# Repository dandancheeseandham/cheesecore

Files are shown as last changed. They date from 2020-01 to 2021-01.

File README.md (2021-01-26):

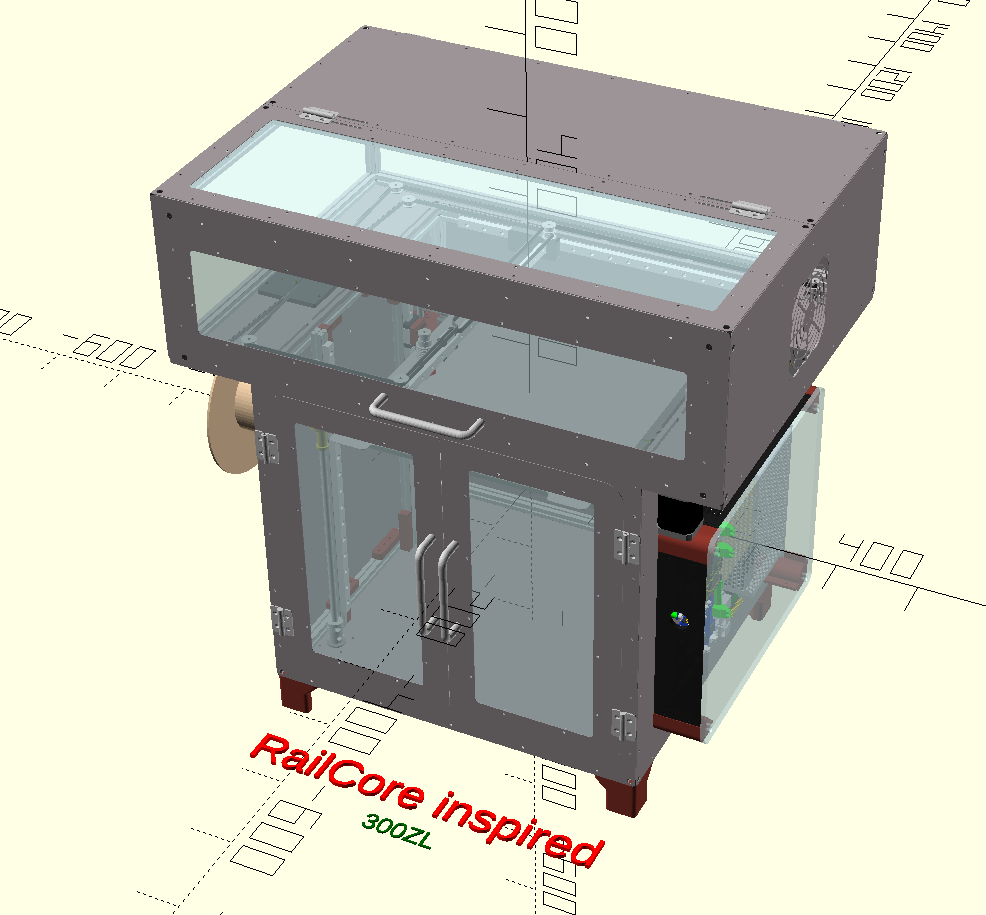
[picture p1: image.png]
Image of cheesecore


# cheesecore - a RailCore II inspired build

This OpenSCAD program has been developed to emulate, and be fully compatible with the RailCore II, but to extend it with parametric functionality. 
While it should be fully compatiable, please note that it is **not a RailCore II**. Because of this **please do not** direct questions about this OpenSCAD code or its models or parts to Tony Akens or J.Steve White. Please discuss with Dan White on Facebook, or idealy cheeseandham on the RailCore Discord.

If you stick with 12mm rails, everything should be fully compatible, but to protect myself I will say **mixing this design with a RailCore II is at your own risk**. 

cheesecore has been developed by cheeseandham / Dan White.

## Initial Goals

To make a RailCore2-compatible parametric OpenSCAD model that includes as standard:- 
 * doors
 * halo
 * top enclosure

The parametrics are to be able to change parameters such as:-
 * frame size (height,width,length) and panel/door thickness
 * extrusion size 
 * rail length and profile (on Z especially) e.g. MGN15
 * lead screw width
 * front window size 
 * electronic box size and electronics placement
 * NEMA stepper motor type (e.g. 17 or 23)

Where possible we stay within the RailCore ecosystem in regards to:-
 * Y carriage - keep 12mm rail on the Y (highest priority)
 * Bed - bed is modifiable
 * Keeping 8mm leadscrews and 12mm rails on Z. This is modifiable.
 
In order to take advantage of existing parts. However these parameters may also be changed - it should be understood that this especially will break compatibility with current machined parts.

## To Do
 * allow >4040 extrusion e.g. 3060 as well as ensuring all screwholes for extrusions are changed.
 * develop main parts of the hotend ecosystem.
 * export a BOM from cheesecore.
 * tidy and optimise the model and code.

### Secondary Goals

1. Adding a RPi as standard, for additional functionality.
 * Bossa for emergency Duet flashing
 * USB and Octoprint (extra features and the ability to communicate with the Duet with a network issue)
 * Extra hardware that a Duet can't support.
 * Automated backups and a simple restore procedure.
2. Include a "advanced user" Duet config and setup.
3. The ability to make modifications and improve the design where appropriate.
The base RailCore design should always be available, and options can be switched on and off as required.
4. Minimize printed part content - metals behave more predictably, espeicially at higher temperatures.
5. Safety - Add software and hardware means (such as TCO's)
6. Aid and ease assembly - anything that can reduce issues in getting it printing reliably. Such as additional parts to ensure squareness of extrusion and rails.

## To use

Some OpenSCAD experience is useful, but if you're comfortable with code in general you should be OK.

 * open a "make*.scad" file to open a whole model.
 * All variables are held in config.scad
 * Theming held in colors.scad and set in prefs.scad
 * Configurations for models are held in models_standard.scad and models_experimentals.scad
 * to play with a whole model, use make_customcore.scad and edit the variables in models_experimental.scad and config.scad regarding the custom model and open with make_customcore.scad
 * core.scad is called to render the model, so you can easily omit parts by using a * to stop it being rendered by editing core.scad/
 * If you open any individual scad part, it will render as per the model in demo.scad , and therefore settings for it in the configuations (models_standard.scad and models_experimentals.scad) (if a individual file contains many parts, you can change its behaviour via editting the demo modile in this part.
 * use the scripts in the build/scripts folder to export the models - this will dump dxfs, stls and renders into the artifacts and renders folders. (any files in artifacts and renders may be deleted as they are easily recreated)
 * hotend is not part of the model yet. It assumes a 12mm rail on Y and RailCore hotend ecosystem at this time.
 * in the build directory are the files to export individual parts.
 * to export all parts, or all parts for all models, just run the appropriate script in build/scripts for your operating system (.cmd for windows, and .sh for mac/linux).

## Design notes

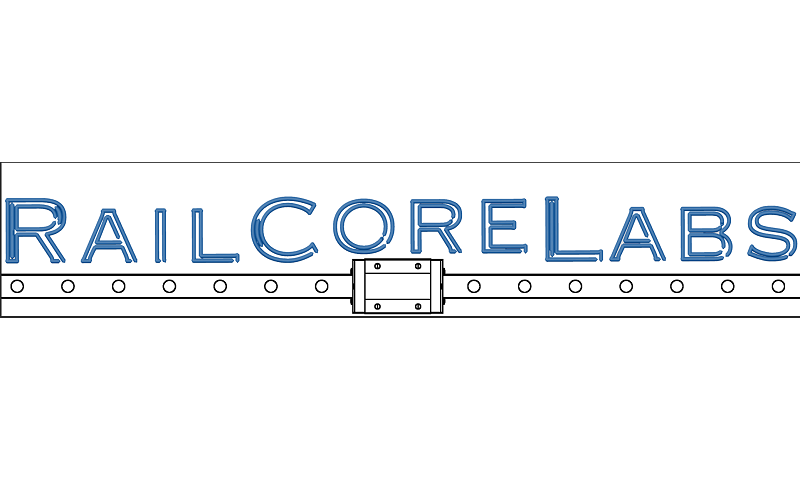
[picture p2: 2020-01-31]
accessories/PanelDue/RailCoreLabs_small.bmp

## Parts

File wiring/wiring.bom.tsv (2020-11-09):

Item | Qty | Unit | Designators
Connector, Delta BFB0524HH Fan, 2 pins | 1 |  | X20
Connector, Ferrule, crimp | 6
Connector, Insulated Female Spade Connector, 6.3 x 0.8mm Tab Size, insulated, 1 pins | 3 |  | X11, X13, X9
Connector, Insulated Ring Terminal, M4 Stud Size, insulated, 1 pins | 11 |  | X1, X10, X12, X2, X22, X3, X4, X5, X6, X7, X8
Connector, Molex 50-57-9404, female, 4 pins | 1 |  | X21
Connector, Molex 70107-0003, male, 4 pins | 1 |  | X18
Connector, Molex KK 254, female, 2 pins | 1 |  | X17
Connector, Molex KK 254, female, 3 pins | 2 |  | X14, X16
Connector, OMRON D2F-01F, Microswitch, 3 pins | 2 |  | X15, X19
Connector, Stripped Wire, 10mm | 9
Wire, 0.25 mm², BK | 1.1 | m | W15, W16
Wire, 0.25 mm², GN | 2.1 | m | W14, W15, W16
Wire, 0.25 mm², GY | 2.1 | m | W14, W15, W16
Wire, 0.25 mm², RD | 1.1 | m | W15, W16
Wire, 1.5 mm², BN | 0.89 | m | W1, W5, W6
Wire, 1.5 mm², BU | 0.7 | m | W1, W10, W11
Wire, 1.5 mm², GN | 2.05 | m | W12, W13, W17, W4
Wire, 1.5 mm², GY | 1.0 | m | W2, W3, W7, W8, W9

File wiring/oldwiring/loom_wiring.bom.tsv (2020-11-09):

Item | Qty | Unit | Designators
Connector, 0.25" Quick Disconnect / 6.3mm female spade F/I terminal / Insulated Crimp Receptacle, insulated, 1 pins | 3 |  | X11, X13, X9
Connector, Delta BFB0524HH Fan, 2 pins | 1 |  | X20
Connector, Ferrule, crimp | 6
Connector, Molex 50-57-9404, female, 4 pins | 1 |  | X21
Connector, Molex 70107-0003, male, 4 pins | 1 |  | X18
Connector, Molex KK 254, female, 2 pins | 1 |  | X17
Connector, Molex KK 254, female, 3 pins | 2 |  | X14, X16
Connector, OMRON D2F-01F, Microswitch, 3 pins | 2 |  | X15, X19
Connector, Ring Terminal RV1.25-5S Stud size 10, insulated, 1 pins | 11 |  | X1, X10, X12, X2, X22, X3, X4, X5, X6, X7, X8
Connector, Stripped Wire, 10mm | 9
Wire, 16 AWG, BK | 1.5 | m | W1, W2, W3, W7, W8, W9
Wire, 16 AWG, GN | 2.05 | m | W12, W13, W17, W4
Wire, 16 AWG, RD | 0.89 | m | W1, W5, W6
Wire, 16 AWG, WH | 0.2 | m | W10, W11
Wire, 24 AWG, BK | 3.2 | m | W14, W15, W16
Wire, 24 AWG, GN | 2.1 | m | W14, W15, W16
Wire, 24 AWG, RD | 1.1 | m | W15, W16

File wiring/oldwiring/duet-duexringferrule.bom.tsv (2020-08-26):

Item | Qty | Unit | Designators
Connector, Ferrule, crimp, 2.0 mm², YE | 1
Connector, Ring#8, crimp, 1 pins | 1 |  | DUET
Cable, 1 x 0.34 mm² | 0.5 | m | BED_SSR3

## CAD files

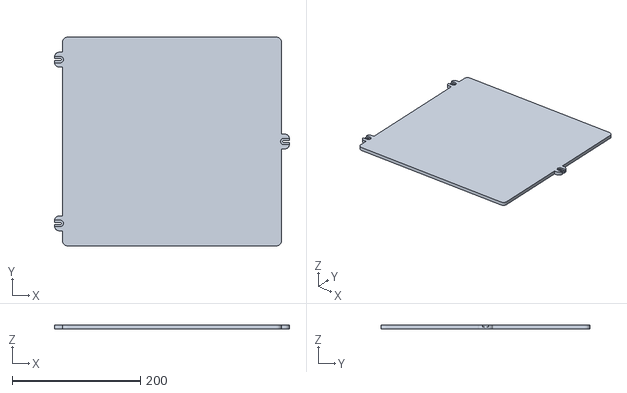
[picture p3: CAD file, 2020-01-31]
accessories/prusa_slicer_configs/railcore.stl
366.0 x 325.0 x 6.35

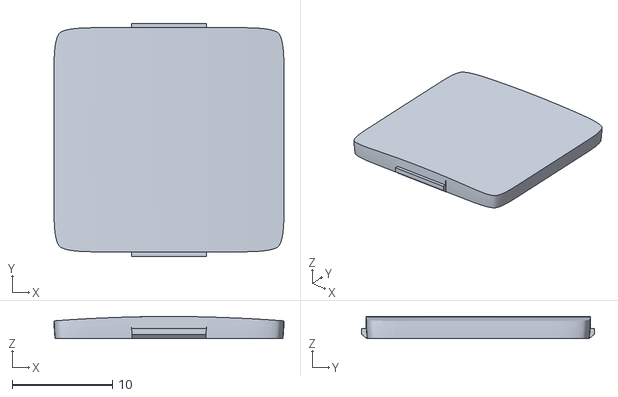
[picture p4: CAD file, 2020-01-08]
nopscadlib/vitamins/microview/GKM-002_R05_CHIP_UPPER_HOUSING-1.STL
22.9 x 23.2 x 2.20

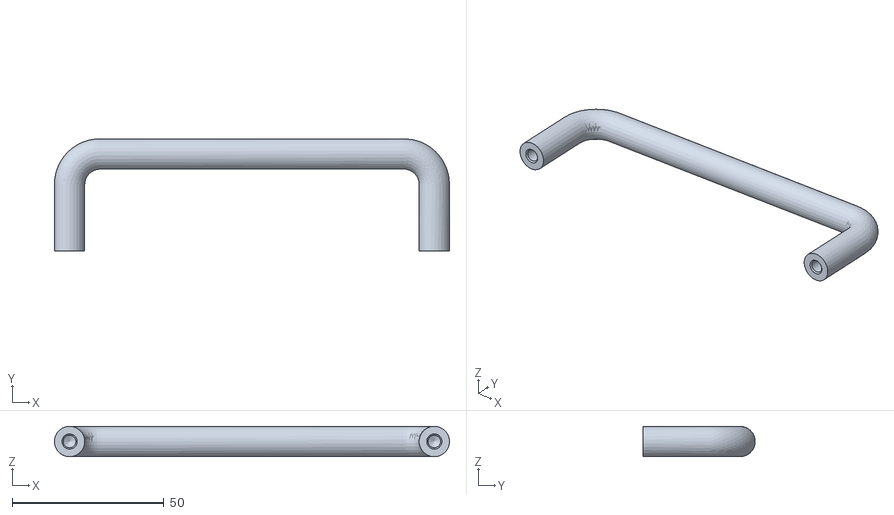
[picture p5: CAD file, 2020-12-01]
UWAN10-120-27.stl
130.0 x 37.0 x 10.0

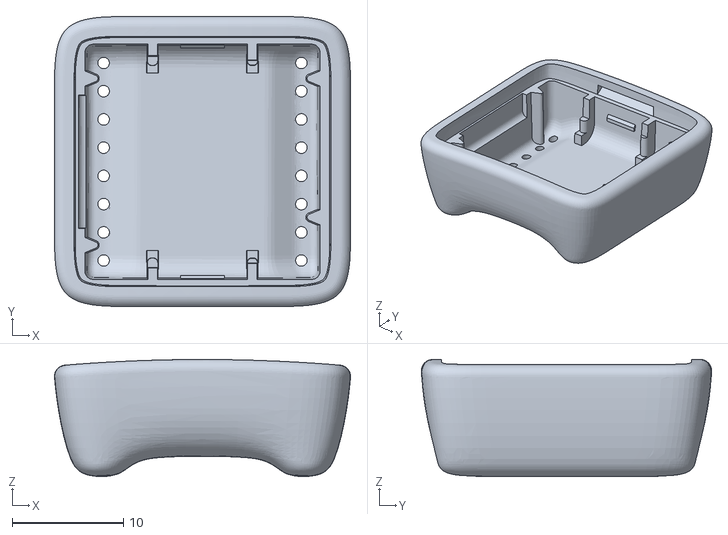
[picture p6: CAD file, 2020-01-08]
nopscadlib/vitamins/microview/GKM-003_R05_CHIP_LOWER_HOUSING.STL
26.7 x 26.1 x 10.5

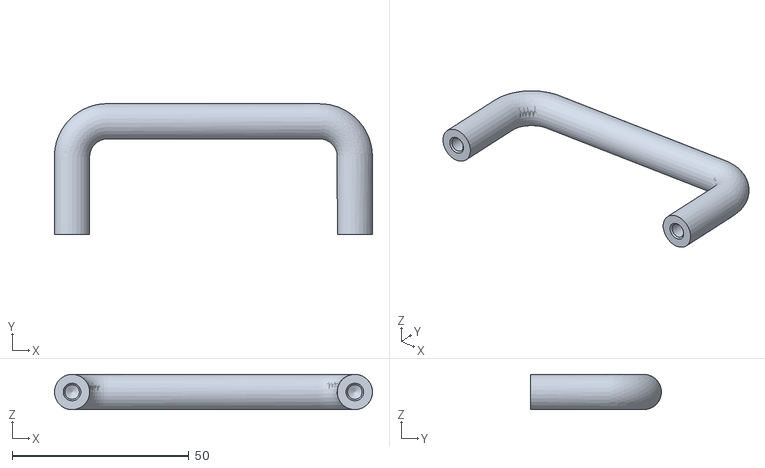
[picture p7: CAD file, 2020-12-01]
UWAN10-80-27.stl
90.0 x 37.0 x 10.0

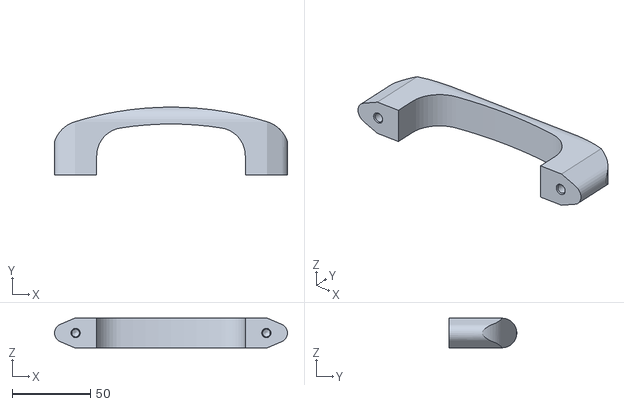
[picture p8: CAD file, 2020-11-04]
HHDS122.stl
149.0 x 43.3 x 19.0

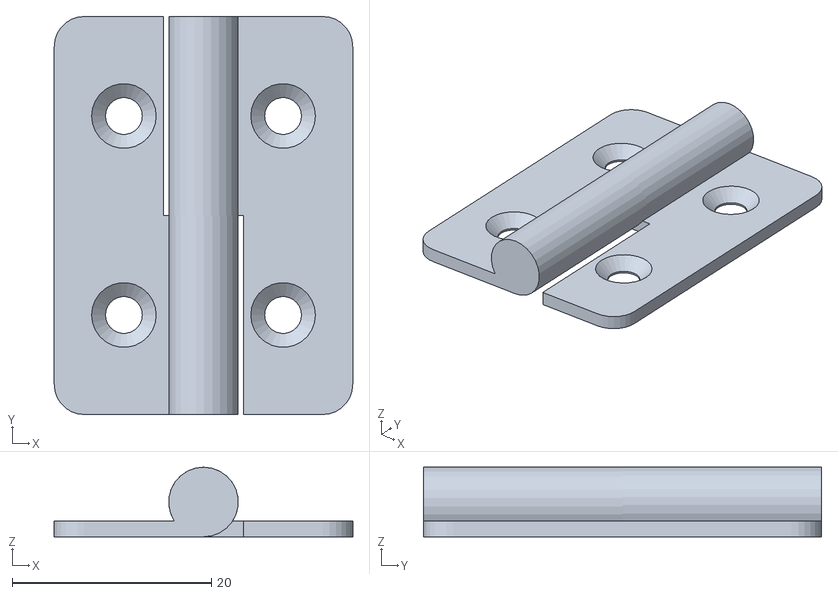
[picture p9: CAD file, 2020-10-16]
B_1075_R.stl
30.0 x 40.0 x 7.00

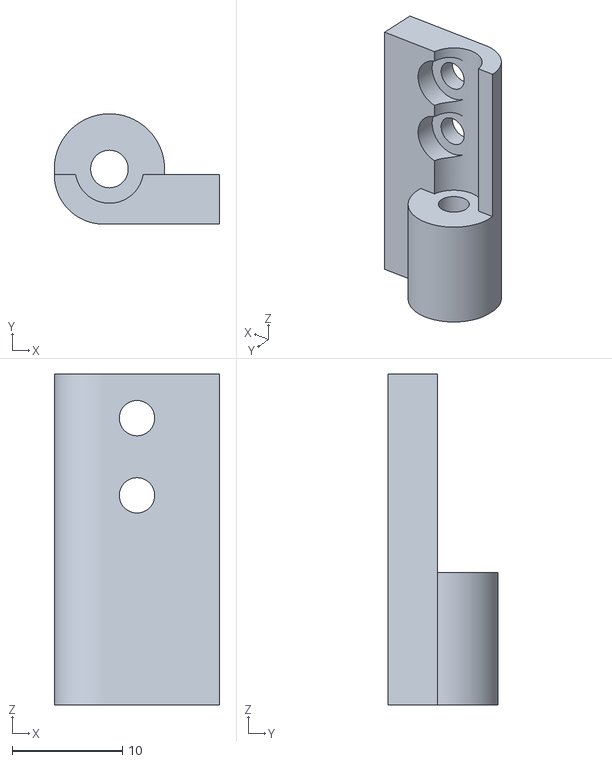
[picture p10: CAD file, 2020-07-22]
HINGE_1.stl
15.0 x 10.00 x 30.0

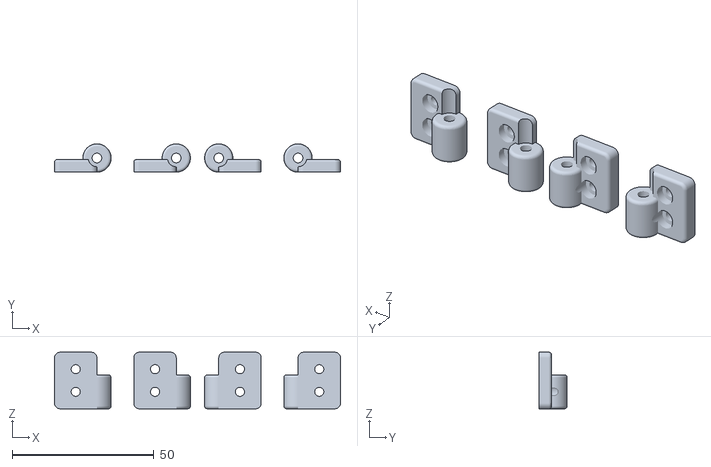
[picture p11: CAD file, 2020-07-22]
HINGE_2.stl
101.0 x 10.0 x 20.0

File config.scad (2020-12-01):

// vim: set nospell:
include <colors.scad>
include <prefs.scad>
include <constants.scad>
use <validation.scad>
include <nopscadlib/vitamins/rails.scad>
include <nopscadlib/vitamins/stepper_motors.scad>

// *************************************************************************************************************************************************

// FRAME - either specify frame size complete or specify extrusion sizes and addon the corner cubes e.g. [15*2,15*2,15*2] for 15mm corner cubes.
//                        sizeX sizeY sizeZ
//Standard
frame_original_rc150mini= [270, 270, 270] + [15*2,15*2,15*2]; // defining extrusion size and then adding frame corner cubes
frame_original_rc250zl  = [400, 370, 360] + [15*2,15*2,15*2];
frame_original_rc300zl  = [460, 425, 415] + [15*2,15*2,15*2];
frame_original_rc300zlt = [460, 425, 715] + [15*2,15*2,15*2];
//Experimental
frame_rc300_custom      = [490, 500, 460];
//Test-ground
frame_rc300zl4040       = [590, 555, 545];


// PANEL - Sides, halo and doors.
//                                  Panel        panel    Extend      Panel Screw  max panel    Bottom
//                                thickness      radius   panels      Offset       screw space  braces?
//Standard
panels_imperial_250zl   = ["PANELS",0.25 * inch,  5,      0,0,0,      42.5,          101,       false];
panels_imperial         = ["PANELS",0.25 * inch,  5,      0,0,0,      50,            100,       true];
panels_metric           = ["PANELS",6,            5,      0,0,0,      50,            100,       true];
panels_aluminium        = ["PANELS",4,            5,      0,0,0,      50,            100,       false];
panels_steel            = ["PANELS",0.8,          5,      0,0,0,      50,            100,       false];
//Experimental
panels_custom           = ["PANELS",6,            5,      150,0,53,   55,            100,       false];
panels_cheese           = ["PANELS",3,            3,      95*2,0,53,  50,            100,       false];
function fitting_error()= 0.25; //reduce panels by this size to account for whatever +- cutting error there may be
function feetheight()   = $feet_depth;

// FRONT WINDOW / DOOR
//                            name                sizeXY   radius   offset    door thickness
//Standard
front_window_original_150mini = ["WINDOW_TYPE", [245, 210], 10,     [0, 5],   0.25 * inch];
front_window_original_250zl   = ["WINDOW_TYPE", [370, 335], 10,     [0, 5],   0.25 * inch];
front_window_original_300zl   = ["WINDOW_TYPE", [420, 385], 10,     [0, 5],   6];
front_window_cheesecore       = ["WINDOW_TYPE", [420, 385], 10,     [0, 5],   0.8];
front_window_original_300zlt  = ["WINDOW_TYPE", [410, 645], 10,     [0, 0],   6];
//Experimental
front_window_custom           = ["WINDOW_TYPE", [420, 385], 10,     [0, 0],   6];

// RAILS
//                           sizeX  Xtype  sizeY  Ytype    sizeZ Ztype
//Standard
rails_original_rc150mini = [[245, MGN12], [245, MGN12], [245, MGN12]];
rails_original_rc250zl   = [[350, MGN12], [350, MGN12], [350, MGN12]];
rails_original_rc300zl   = [[400, MGN12], [400, MGN12], [400, MGN12]];
rails_original_rc300zlt  = [[400, MGN12], [400, MGN12], [700, MGN12]];
//Experimental
rails_misumi_395         = [[395, MGN12], [395, MGN12], [395, MGN12]];
rails_misumi_420         = [[420, MGN12], [420, MGN12], [420, MGN12]];
rails_misumi_420XY_470Z  = [[420, MGN12], [420, MGN12], [470, MGN12]];
rails_rc300zlt_high_temp = [[400, MGN12], [400, MGN12], [700, MGN15]];
// Test-ground (can be deleted)
rails_300zl_4040         = [[500, MGN15], [500, MGN12], [500, MGN15]];
rails_custom             = [[420, MGN9] , [445, MGN12], [420, MGN15]];

// ELECTRONICS BOX ALONG WITH  & ELECTRONICS & CABLE PLACEMENT -  placement of parts on right panel with X/Y as centre
//                                                      DIMENSIONS               |       POSITIONS
//                           name        sizeX  sizeZ  depth thick, move lasercut   cable_bundle      DuetE            Duex            PSU        SSR            RPi
//                                                                  box
//Standard                                                         down
elecbox_original_rc150mini= ["ELEC.BOX", 298.9, 238.9, 60 ,   6,    25,    true,   [-84,126.5,0], [-84.82,50.5,0], [-84.82,-59.5,0], [90,30,0], [45,-115,0] , [90,30,0]] ;
elecbox_original_rc250zl  = ["ELEC.BOX", 298.9, 238.9, 60 ,   6,    25,    true,   [-400/2+106.68,390/2-101+25], [-84.82,50.5,0], [-84.82,-59.5,0], [90,30,0], [45,-115,0] , [90,30,0]] ;
elecbox_original_rc300zl  = ["ELEC.BOX", 298.9, 238.9, 60 ,   6.5,    25,    true,   [-84,126.5,0], [-84.82,50.5,0], [-84.82,-59.5,0], [60,25,0], [140,60,0] , [50,-110,0]] ;
elecbox_original_rc300zlt = ["ELEC.BOX", 298.9, 438.9, 60 ,   6,    25,    true,   [-84,226.5,0], [-84.82,150.5,0],[-84.82,40.5,0],  [80,75,0], [0,-110,0]  , [-90,-140,0]] ;
//Experimental
//elecbox_300_large         = ["ELEC.BOX", 350,   290,   59,    1,    25,    true,   [-84,146.5,0], [-85-15,70,0],      [-85-15,-40,0],      [70,30,0],[160,70,0] , [-20+80,-86-40,0]] ;
elecbox_300_large         = ["ELEC.BOX", 298,   330,   60,    1,    0,    true,   [-84,146.5,0], [-85-15,70,0],      [-85-15,-40,0],      [70,30,0],[160,70,0] , [-20+80,-86-40,0]] ;
elecbox_300_Duet3         = ["ELEC.BOX", 298.9, 238.9, 60 ,   6,    25,    true,   [-84,126.5,0], [-84.82,50.5,0], [-84.82,-69.5,0], [90,30,0], [45,-115,0] , [-70,-60,0]] ;
// Test-ground (can be deleted)
//elec_cheesecore           = ["ELEC.BOX", 350,   290,   59+(95-59),    6,    25,    true,   [-84,146.5,0], [-85,70,0],      [-85,-40,0],      [70,30,0],[160,70,0] , [-90,-130,0]+[-71,36,0]] ;
elec_cheesecore           = ["ELEC.BOX", 290,   290,   60,    6,    25,    true,   [-84,146.5,0], [-85,70,0],      [-85,-40,0],      [70,30,0],[160,70,0] , [-90,-130,0]+[-71,36,0]] ;
elec_cheesecore2          = ["ELEC.BOX", 330,   290,   60,    6,    25,    true,   [-84,146.5,0], [-85,70,0],      [-85,-40,0],      [70,30,0],[160,70,0] , [-90,-130,0]+[-71,36,0]] ;
elec_cheesecore3          = ["ELEC.BOX", 350,   290,   60,    6,    35,    true,   [-84,126.5,0], [-84.82,50.5,0], [-84.82,-59.5,0], [60,25,0], [140,60,0] , [0,0,0]] ;
elec_miniplaceh           = ["ELEC.BOX", 118.9, 58.9,  60 ,   6,    25,    true,   [-84,126.5,0], [-84.82,50.5,0], [-84.82,-59.5,0], [60,00,0],  [145,50,0] , [-90,-140,0]] ;
elec_custom               = ["ELEC.BOX", 410,   310,   60 ,   6,    25,    false,  [-84,146.5,0], [-85,70,0],      [-85,-40,0],      [90,30,0], [70,-130,0] , [-90,-140,0]] ;
elec_rc300zltwithcheese   = ["ELEC.BOX", 445-32,380,   60 ,   6,    60,    true,   [-84,146.5,0], [-85,70,0],      [-85,-40,0],      [100,50,0],[80,-110,0] , [-90,-130,0]] ;
// +[80,-40,13+5] pi?
filament_box_cheesecore  =  ["ELEC.BOX", 370,   360,   95,   6];

function filament_box_size_y()             = $filament_box[1] ;
function filament_box_size_z()             = $filament_box[2] ;
function filament_box_depth()              = $filament_box[3] ;
function filament_box_acrylic_thickness()  = $filament_box[4] ;

function back_panel_enclosure()            = false;  // is there an additional electronics box on the rear panel? FIXME: FInish off and allow conduit holes.

// HALO - Just XYZ at the moment. Z is panel thickness
//                        XY
//                      addition
//Standard, halo for 250ZL,300ZL and 300ZLT is the same
halo_rc150mini                = [125  ,0,  4];
//halo_rc                     = [75*2 ,0,  4];
halo_rc_old                   = [75*2 ,15, 4];  // I've made the standard size larger than it needs to be by 40mm in order to accommodate NEMA23 and a single enclosure size
halo_rc                       = [100*2,30, 6];
//Experimental
halo_rc_NEMA23                = [95*2 ,30, 4];
halo_rc_cheese                = [80*2 ,15, 4];
//(prechanged) halo_rc_cheese_mod            = [80*2 ,30, 6];
halo_rc_cheese_mod            = [100*2,30, 6];
halo_rc_dans_ZLT              = [74*2 ,10, 4];
function halo_back_overhang() = false ; //apply Y extra only to the back of the halo for top enclosure mounting

// ENCLOSURE BOX - size and shape - can be defined as unconstrained from the frame, or constrained using halo variables.
//                             X  Y   Z
//Standard
enclosure_rc_standard          = [0, 0, 200];
//Experimental
enclosure_large                = [0, 0, 245];
enclosure_custom               = [0, 0, 200];

function enclosure_height_above_frame() = 0 ; // For the printed interface arrangement. Uneeeded with the cheesecore halo. but Left for backwards compatibility.
// FIXME: X and Y are pointless. Integrate enclosure height above frame too.
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

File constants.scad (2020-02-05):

epsilon=0.1;  // epislon value for OpenSCAD reasons :)
inch = 25.4; // convert imperial units
doorgap = 0 ; // gap between doors

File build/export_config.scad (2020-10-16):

// vim: set nospell:
use <../models_standard.scad>
use <../models_experimental.scad>
use <../models_test_ground.scad>
module export_artifacts() {
  300ZL_2020()
   children();
}

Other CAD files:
misumi/B-1075_L.stl
nopscadlib/global_defs.scad
LCD-box-mount.scad
PanelDueEnclosure.scad
Untitled.scad
accessories/calibration.scad
accessories/prusa_slicer_configs/Overlay.scad
anti-backlash-nut.scad
bearing_block.scad
bed.scad
build/bearing_block.stl.scad
build/bed.dxf.scad
build/bed.stl.scad
build/bed_steel_sheet.dxf.scad
build/bed_steel_sheet.stl.scad
build/door_knob.stl.scad
build/door_single.dxf.scad
build/door_single.stl.scad
build/door_single_mirror.dxf.scad
build/electronics_box_corner.stl.scad
build/electronics_box_cover.dxf.scad
build/electronics_box_cover.stl.scad
build/electronics_box_panel_bottom.dxf.scad
build/electronics_box_panel_bottom.stl.scad
build/electronics_box_panel_left_side.dxf.scad
build/electronics_box_panel_left_side.stl.scad
build/electronics_box_panel_right_side.dxf.scad
build/electronics_box_panel_right_side.stl.scad
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

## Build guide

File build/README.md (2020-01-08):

# Cheesecore Build Artifact Export

Use `export_artifacts` to export OpenSCAD files under `build/` into dxf or stl files under `artifacts/`

Each file under `build/` is setup to export one artifact file.  The exported file will have the same filename as the file under `build/`, with the `.scad` extension removed.

When adding new files, we need to ensure that any stl is exported in the preferred printing orientation so that the object need not be rotated in the slicer. This should include considerations of where the seam will appear on the part.

To export a different model, edit the `export_artifacts()` module in `export_config.scad` to call the model you want to export.  (Hopefully future OpenSCAD changes will let us skip this step).

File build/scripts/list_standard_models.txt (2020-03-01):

railcore_300ZL_compatible
railcore_300ZLT_compatible
railcore_250ZL_compatible
railcore_150_compatible

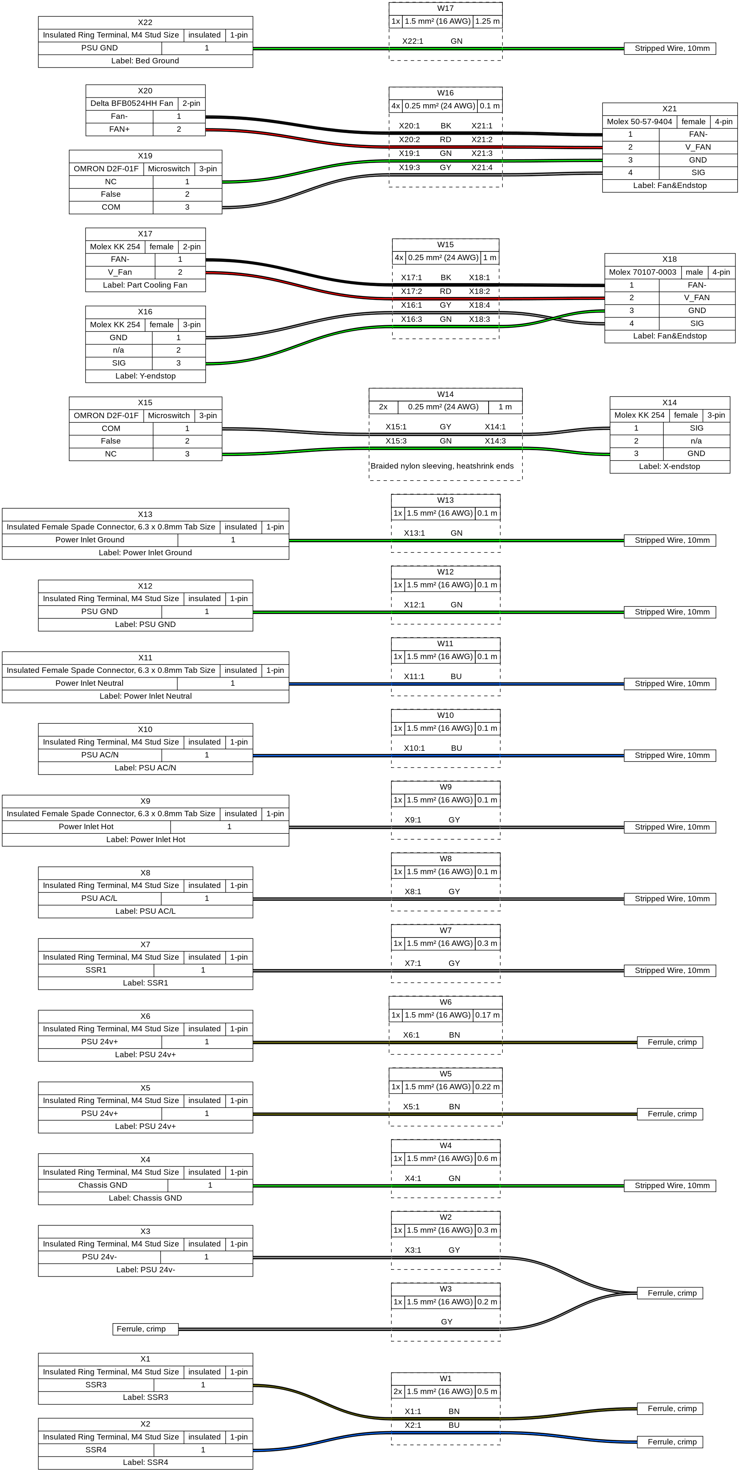
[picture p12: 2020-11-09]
wiring/wiring.png

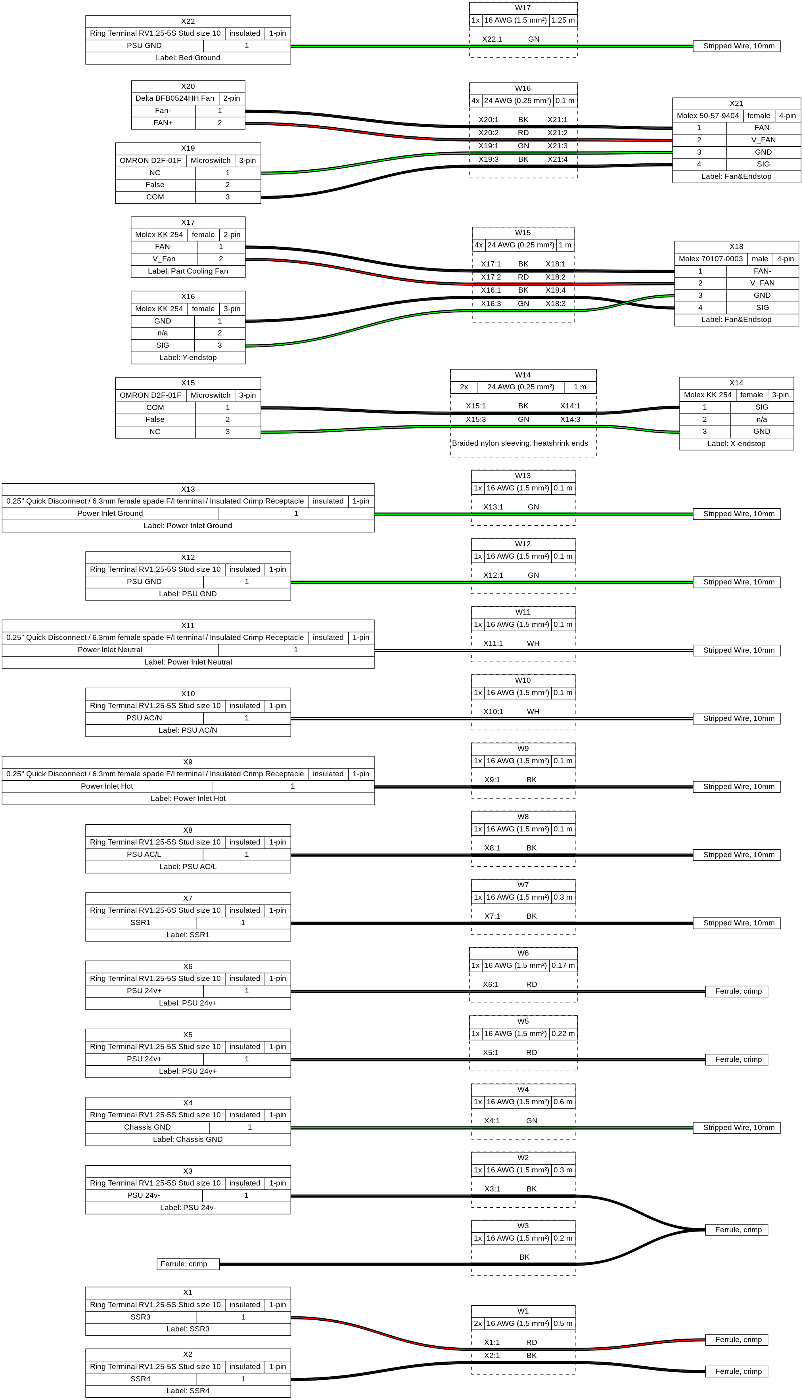
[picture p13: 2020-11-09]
wiring/oldwiring/loom_wiring.png

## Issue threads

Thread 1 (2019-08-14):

Initial thoughts and to-dos

dandancheeseandham, 2019-08-14:
- [x] sort out attribution for extrusions (or recode) - I guess a cube will do for now, but I do like seeing "real extrusions" so lets leave it in for as long as possible.
- [x] "railstls" folder have been brought in, and are for "internal" use. I'm guessing the creative commons license it is under is incompatible with GPL, but it's useful to have these while developing. Assume they won't be there in the end.
- [x] Will also have to decide what is worth replicating, and what isn't. e.g. replace zbackets with corner cubes instead? Some things will have to be parametric anyway, such as X carriage if allowing bigger rails.

As well as railcore compatibility. I'd also like a secondary goal of 2020 extrusion, 15mm rails (bar Y) and 10mm lead screws.

Closed 2020-01-28.

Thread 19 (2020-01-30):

$panels problems

dandancheeseandham, 2020-01-30:
Currently in config.scad there is the lines from line 37
```
function side_panel_thickness()     = 2 ; // $panels[1]
function panel_radius()             = 5; // $panels[2]
```

When a make_railcore300zlcompatible.scad is run (this is the one I've tested with, it does the same with others), there is output from core.scad these lines
```
  echo ("$panels[1]: ",$panels[1]);
  echo ("side_panel_thickness(): ",side_panel_thickness() );
  echo ("$panels: ",$panels);
```
to the tune of
```
ECHO: "$panels[1]: ", 6.35
ECHO: "side_panel_thickness(): ", 2
ECHO: "$panels: ", ["PANELS", 6.35, 5, 6.35, 0, 50]
```

if line 37 in config.scad is changed to
```
function side_panel_thickness()     = $panels[1] ;
```
the output breaks, no printer is rendered and the first error is
```
WARNING: Ignoring unknown variable '$panels', in file config.scad, line 37.
```
Except it is defined and is seen in the output echoed.

It seems "function panel_radius()" can be changed to "$panels[2]" though!

lostapathy, 2020-02-05:
I created [this branch](https://github.com/lostapathy/cheesecore/tree/panel_issue) to replicate the issue.  By the time I got to this the line numbers had already changed.  Going forward, just for the sake of clarity and expediency, it's probably worth having the reporter create and publish this type of branch that shows issues like this and then referencing it in the issue.

lostapathy, 2020-02-05:
The error actually comes from [this block](https://github.com/lostapathy/cheesecore/blob/panel_issue/config.scad#L97).  Since that code is defined right in config.scad (and not in a module/function), it gets evaluated when the file is processed, and outside the scope of any printer definitions that would define the special $panels variable.

I would fix this by basically removing all of those definitions, and making a function to the effect of that calculated the halo size at runtime based on the machine definition, and not trying to build that up in the config.  I can help you work through that, but I need to get back up to speed on other code changes first to really understand what's going on.

lostapathy, 2020-02-05:
As far as how to troubleshoot this type of error - I commented out the line generating the warning.  That causes an error to be thrown by the caller of the problematic function ("Ignoring unknown function").  You can then look at the caller(s) that are throwing errors and in this case it was pretty obvious why $panels wasn't defined where you expected it to be.

Closed 2020-02-05.

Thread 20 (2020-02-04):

Flexplate is "Mixing 2D and 3D objects"

dandancheeseandham, 2020-02-04:
The nice curve on the tab gets ignored when full rendered.
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

```
WARNING: Mixing 2D and 3D objects is not supported, in file ../bed.scad, line 135
WARNING: Ignoring 2D child object for 3D operation, in file ../bed.scad, line 135
```
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

I tried to fix it with linear extrude, but couldn't find a working approach.

lostapathy, 2020-02-05:
Your error trace shows the error is in ../bed.scad - would be helpful to reproduce things like this if you specified what file you were running to actually trigger this.

Closed 2020-02-05.

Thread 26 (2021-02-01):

Move PSU

dandancheeseandham, 2021-02-01:
Move PSU and SSR under the bottom of the printer.  Build a box around that all, with a faceplate that's flush with the right side panel we have now.  Bed heater would go straight down into that (through a connector) and not through the ebox.  On the faceplate facing the e-box, we'd have connectors for 12v (and maybe a spot for 5v) to get power out of it, as well as a connector to control the SSR.
Then extend the ebox down to where it covers that faceplate so you can access those ports inside the box.
At that point we've moved all the mains wiring out of the ebox, freed up a fuckton of space and not spent much money

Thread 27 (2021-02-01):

move loom hole into halo

dandancheeseandham, 2021-02-01:
Modular halo has a plate for improvements, one change is to add a hole in the plate (and one in the top of the electronics box I guess) and allow loom to flow in that direction.
then remove hole in right side panel

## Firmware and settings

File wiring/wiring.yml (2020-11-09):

connectors:
  X1:
    pinout: [SSR3]
    type: Insulated Ring Terminal, M4 Stud Size
    subtype: insulated
    notes: "Label: SSR3"
  X2:
    pinout: [SSR4]
    type: Insulated Ring Terminal, M4 Stud Size
    subtype: insulated
    notes: "Label: SSR4"
  F_10_1: # manually define a ferrule (with unique designator)
    category: ferrule
    type: Ferrule, crimp
    notes: Duet Bed+
  F_10_2: # manually define a ferrule (with unique designator)
    category: ferrule
    type: Ferrule, crimp
    notes: Duet Bed-
    
  X3:
    pinout: [PSU 24v-]
    type: Insulated Ring Terminal, M4 Stud Size
    subtype: insulated
    notes: "Label: PSU 24v-"
  F_10_3: # manually define a ferrule (with unique designator)
    category: ferrule
    type: Ferrule, crimp
    notes: Duet Vin-
  F_10_4: # manually define a ferrule (with unique designator)
    category: ferrule
    type: Ferrule, crimp
    notes: Duet Vin-

    
  X4:
    pinout: [Chassis GND]
    type: Insulated Ring Terminal, M4 Stud Size
    subtype: insulated
    notes: "Label: Chassis GND"
  F_10_5: # manually define a ferrule (with unique designator)
    category: ferrule
    type: Stripped Wire, 10mm
    notes: WAGO Ground Block

  X5:
    pinout: [PSU 24v+]
    type: Insulated Ring Terminal, M4 Stud Size
    subtype: insulated
    notes: "Label: PSU 24v+"
  F_10_6: # manually define a ferrule (with unique designator)
    category: ferrule
    type: Ferrule, crimp
    notes: Duet Vin+

  X6:
    pinout: [PSU 24v+]
    type: Insulated Ring Terminal, M4 Stud Size
    subtype: insulated
    notes: "Label: PSU 24v+"
  F_10_7: # manually define a ferrule (with unique designator)
    category: ferrule
    type: Ferrule, crimp
    notes: Duex Vin+

  X7:
    pinout: [SSR1]
    type: Insulated Ring Terminal, M4 Stud Size
    subtype: insulated
    notes: "Label: SSR1"
  F_10_8: # manually define a ferrule (with unique designator)
    category: ferrule
    type: Stripped Wire, 10mm
    notes: WAGO AC Hot Block

  X8:
    pinout: [PSU AC/L]
    type: Insulated Ring Terminal, M4 Stud Size
    subtype: insulated
    notes: "Label: PSU AC/L"
  F_10_9: # manually define a ferrule (with unique designator)
    category: ferrule
    type: Stripped Wire, 10mm
    notes: WAGO AC Hot Block
    
  X9:
    pinout: [Power Inlet Hot]
    type: Insulated Female Spade Connector, 6.3 x 0.8mm Tab Size
    subtype: insulated
    notes: "Label: Power Inlet Hot"
  F_10_10: # manually define a ferrule (with unique designator)
    category: ferrule
    type: Stripped Wire, 10mm
    notes: WAGO AC Hot Block
    
  X10:
    pinout: [PSU AC/N]
    type: Insulated Ring Terminal, M4 Stud Size
    subtype: insulated
    notes: "Label: PSU AC/N"    
  F_10_11: # manually define a ferrule (with unique designator)
    category: ferrule
    type: Stripped Wire, 10mm
    notes: WAGO AC Neutral Block
    
  X11:
    pinout: [Power Inlet Neutral]
    type: Insulated Female Spade Connector, 6.3 x 0.8mm Tab Size
    subtype: insulated
    notes: "Label: Power Inlet Neutral"
  F_10_12: # manually define a ferrule (with unique designator)
    category: ferrule
    type: Stripped Wire, 10mm
    notes: WAGO AC Neutral Block

  X12:
    pinout: [PSU GND]
    type: Insulated Ring Terminal, M4 Stud Size
    subtype: insulated
    notes: "Label: PSU GND"
  F_10_13: # manually define a ferrule (with unique designator)
    category: ferrule
    type: Stripped Wire, 10mm
    notes: WAGO AC Ground Block
    
  X13:
    pinout: [Power Inlet Ground]
    type: Insulated Female Spade Connector, 6.3 x 0.8mm Tab Size
    subtype: insulated
    notes: "Label: Power Inlet Ground"
  F_10_14: # manually define a ferrule (with unique designator)
    category: ferrule
    type: Stripped Wire, 10mm
    notes: WAGO AC Ground Block
    
  X14:
    type: Molex KK 254
    subtype: female
    pinout: [SIG, n/a, GND]
    notes: "Label: X-endstop"
  X15:
    pinout: [COM, NO, NC]
    type: OMRON D2F-01F 
    subtype: Microswitch

  X16:
    type: Molex KK 254
    subtype: female
    pinout: [GND, n/a, SIG]
    notes: "Label: Y-endstop"
  X17:
    type: Molex KK 254
    subtype: female
    pinout: [FAN-, V_Fan]
    notes: "Label: Part Cooling Fan"
  X18:
    type: Molex 70107-0003
    subtype: male
    pinout: [FAN-, V_FAN, GND, SIG]
    notes: "Label: Fan&Endstop"

  X19:
    pinout: [NC, NO, COM]
    type: OMRON D2F-01F 
    subtype: Microswitch
  X20:
    type: Delta BFB0524HH Fan
    pinout: [Fan-, FAN+]
  X21:
    type: Molex 50-57-9404
    subtype: female
    pinout: [FAN-, V_FAN, GND, SIG]
    notes: "Label: Fan&Endstop"

  X22:
    pinout: [PSU GND]
    type: Insulated Ring Terminal, M4 Stud Size
    subtype: insulated
    notes: "Label: Bed Ground"
  F_10_15: # manually define a ferrule (with unique designator)
    category: ferrule
    type: Stripped Wire, 10mm
    notes: WAGO AC Ground Block
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

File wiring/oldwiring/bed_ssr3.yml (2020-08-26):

connectors:
  DUET:
    category: Ring
    type: Ring#8, crimp
    pincount: 1
  SSR: # manually define a ferrule (with unique designator)
    category: ferrule
    type: Ferrule, crimp
    subtype: 2.0 mm²
    color: YE

cables:
  BED_SSR3:
    wirecount: 1
    length: 0.5
    gauge: 0.34 mm2
    show_equiv: true # auto-calculate AWG equivalent
    colors: [RD]
connections:
  -
    - DUET: [1]
    - BED_SSR3: [1]
    - SSR: [1]

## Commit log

2020-01-14 build notes generation and change panel_thickness var to side_panel_thickness
    [config.scad, core.scad, corexy_belts.scad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]
2020-01-14 minor updates
    [bearing_block.stl, config.scad, door - single.dxf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]
2020-01-14 update reporting
    [core.scad, halo.scad]
2020-01-16 magnums and top enclosure work
    [colors.scad, config.scad, core.scad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]
2020-01-17 improve top enclosure
    [config.scad, constants.scad, core.scad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]
2020-01-21 Improvements to build dir, enclosure and z-yoke
    Z yoke now has parametric screw size and pcd derived from config
    Enclosure improvments: created door and shuffled existing extrusion to better fit
    [bearing_block.stl.scad, bed.dxf.scad, bed.stl.scad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]
2020-01-22 minor yoke updates
    [rails.scad, z-yoke.scad, z-yoke6.scad]
2020-01-24 Duet3 & Top enclosure
    Working on fan guard for top enclosure
    [bed.scad, config.scad, core.scad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]
2020-01-25 Z motor is not necessarily NEMA17
    [z-tower.scad]
2020-01-25 Make Z motor hole pattern depend on motor type
    [side_panels.scad]
2020-01-29 Updates to sidepanels, feet, halo and tidy config
    [Bondtech BMG mount.iges, config.scad, core.scad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]
2020-01-29 sort out feet
    [config.scad, halo.scad, models_experimental.scad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]
2020-01-30 flex plate for bed
    [bed.scad]
2020-01-30 position bed in assembly
    [bed.scad, core.scad]
2020-01-30 cleaning up
    fix build folder issues
    further config.scad tidying
    reenable modules in core and add comments
    change demo to 300zl
    add ability to move electronics box down from centre to give motors more space and use the space below the box.
    fix idlers spacer name
    fix windows scripts for building
    side panels - add extending and additional back electronics box
    z-yoke6.scad - experimental z-yoke, not parametric
    [Bondtech BMG mount.iges, bearing_block.stl, bed.dxf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]
2020-01-30 remove some comments
    fairly safe update, straight to master
    [bed.scad, config.scad, electronics_box_panels.scad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]
2020-01-31 gentle tidying up
    [bed.scad, config.scad, coupler.scad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]
2020-01-31 change extend variable
    to more appropriate letter
    [config.scad, side_panels.scad]
2020-01-31 add accessories
    [0_Truelevel_and_Mesh_Heated.g, 0_Truelevel_and_Mesh_No_Heat.g, 1_Duet_power_output_OFF.g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]
2020-02-03 panels mod and additional experimental model.
    Extending panels
    Panel rendering depending on extension configuration.
    Ensure fan grill stays at the right position for Duet no matter what size the panels.
    new config "rc300zlwithcheese"
    [config.scad, core.scad, electronics_box_panels.scad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]
2020-02-04 improved fan guard cutouts
    using nopscadlib
    change top enclosure material configuration.
    [anti-backlash-nut.scad, config.scad, door_hinge.scad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]
2020-02-04 Tidy bed.scad
    [bed.scad]
2020-02-05 fix error from mixing 2d and 3d operations
    [bed.scad]
2020-02-05 Tidy colors.scad
    [colors.scad]
2020-02-05 Fixs panels bug
    also remove artifacts from Z bracket by re-adding the render() that was removed previously.
    [config.scad, z-bracket.scad]
2020-02-05 tidying variable names and tabs
    [config.scad, constants.scad, core.scad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]
2020-02-05 clean bottom brace code
    [config.scad, core.scad, frame.scad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]
2020-02-07 massive update, refactored electronics box
    [config.scad, core.scad, electronics_box_assembly.scad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]
2020-02-13 cleaning code
    [bearing_block.stl, bed.dxf, bed.stl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]
2020-02-14 RRF3 and improved export scripting
    [PLA-cooling.g, PLA-start.g, bearing_block.stl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]
2020-02-14 test squash
    [0_Truelevel_and_Mesh_No_Conditions.g, 1_T0_Off.g, 3_Bed_at_top.g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]
2020-02-19 Move electronics box out by side panel thickness
    [electronics_box_assembly.scad, export_config.scad, make_cheesecore_300zl.scad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]
2020-02-23 minor corrections
    [demo.scad, models_standard.scad]
2020-03-01 filament holder
    [coupler.scad, filament_holder.scad, foot.scad]
2020-03-03 commit changes
    [config.scad, core.scad, electronics_box_panels.scad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]
2020-03-03 commit here
    [config.scad, core.scad, electronics_box_assembly.scad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]
2020-03-06 door panel holes for hinges
    minor fix on door hinge
    sort out raspberry pi fitting
    get holes in door panel sorted out
    removing # lines for bugtesting
    [bed.scad, config.scad, core.scad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]
2020-03-06 filament holder error through teardrop
    hack fix
    [filament_holder2kg.scad]
2020-03-06 filament box changes
    [config.scad, electronics_box_assembly.scad, electronics_box_panels.scad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]
2020-03-06 comment for halo
    [config.scad, models_experimental.scad]
2020-03-06 minor adjustments
    [filament_holder.scad, side_panels.scad]
2020-03-06 move electornics box fans slightly
    [electronics_box_panels.scad]
2020-05-12 update after 2 months
    [bearing_block.scad, models_standard.scad, side_panels.scad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]
2020-06-05 add paneldue enclosure and mount
    [LCD-box-mount.scad, PanelDueEnclosure.scad]
2020-06-09 update linux
    [bed.scad, config.scad, core.scad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]
2020-07-07 more updates
    [config.scad, core.scad, extrusion_spacers.scad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]
2020-07-22 commit current
    [0_Truelevel_and_Mesh_Heated.g, 0_Truelevel_and_Mesh_No_Conditions.g, 0_Truelevel_and_Mesh_No_Heat.g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]
2020-08-26 awful practices of committing by cheeseandham
    [config.scad, core.scad, door_single_mirror.dxf.scad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]
2020-10-16 major update
    [B-1075_L.stl, B_1075_R.stl, bearing_block.scad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]
2020-10-16 minor fix
    [config.scad, electronics_box_panels.scad]
2020-11-02 massive update
    [bed.scad, colors.scad, config.scad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]
2020-11-02 switch off filament box for release
    [electronics_box_assembly.scad]
2020-11-05 remove absolute path names to imported STLS
    [top_enclosure_parts.scad, top_enclosure_side_panels.scad]
2020-11-05 add description
    [core.scad, door_hinge.scad, halo2.scad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]
2020-11-09 update wiring
    [core.scad, door_hinge.scad, duet-duexringferrule.bom.tsv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]
2020-12-01 latest update
    [UWAN10-120-27.stl, UWAN10-80-27.stl, config.scad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]
2020-12-02 one handle
    [side_panels.scad, top_enclosure_parts.scad, top_enclosure_side_panels.scad]
2021-01-26 add image
    [electronics_box_assembly0.scad, side_panel.scad, side_panels.scad]
2021-02-01 fix corner cube holes on halo2
    [halo2.scad, side_panels.scad]
